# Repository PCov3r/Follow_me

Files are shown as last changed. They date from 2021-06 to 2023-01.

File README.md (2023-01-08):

# Follow me

***Follow me*** est un projet de première année d'école d'ingénieur créé par 9 étudiants.<br>
Le but est de suivre une personne grâce à un algorithme de reconnaissance faciale et de faire du streaming. On utilise ainsi une raspberry, une carte STM32 et 2 servo-moteurs (un pour le pan et un pour le tilt).<br> On a également implémenté un contrôle manuel du tracking par le biais d'API coté serveur et d'une autre raspberry et d'une STM32 coté commande.

## Serveur et streaming

[Section relative au serveur flask et au tracking](WebServer/FlaskServer/)

Nous avons utilisé la librairie OpenCV pour faire du tracking et la librairie Flask pour implémenter le serveur web et le streaming.<br>

### Tracking et API

La librairie OpenCV possède de manière native différents trackers, dont les détails peuvent être trouvés [ici](https://learnopencv.com/object-tracking-using-opencv-cpp-python/) et [ici](https://ehsangazar.com/object-tracking-with-opencv-fd18ccdd7369). Dans notre cas, nous utilisons le tracker KCF qui est non seulement précis, mais qui retrouve également la personne si celle-ci sort et rentre dans le champ de la caméra. <br>
Le passage du mode tracking automatique au mode contrôle manuel est assuré par le biais d'[API](https://flask.palletsprojects.com/en/2.0.x/api/) sous forme de requêtes HTTP. Le serveur Flask reçoit ces requêtes, en analyse les arguments, et agit en conséquence.
<br>
### Communication avec la carte STM32

La communication entre la Raspberry Pi et la carte STM32 gérant la caméra et les servo-moteurs se fait via le protocole [UART](https://www.raspberrypi.org/documentation/configuration/uart.md). Des détails sur le protocole mis en place se trouvent dans la section relative au contrôle des servos.
Il est à noter que le contrôle des mouvements est pour le moment très naïf. En effet, on indique simplement à la STM32 dans quelle direction on souhaite orienter la caméra. 
<br>
Nous avons en effet abandonné l'idée d'indiquer précisément à la carte la position relative de l'utilisateur, ceci pour des raisons de simplicité et surtout de temps.
Une source d'amélioration serait ainsi d'implémenter cela et d'agir en conséquence sur la vitesse de déplacement afin de s'assurer de ne jamais perdre l'utilisateur.
<br>
### Liste des packages à installer pour le serveur web et tracking

pip : ``sudo apt-get install python3-pip`` <br>
imutils : ``pip3 install imutils`` <br>
opencv : ``apt-get install python3-opencv``<br>
flask : ``pip3 install flask``

<br>
<br>

## Contrôle des mouvements de la caméra

[Section relative au contrôle des mouvements de la caméra](/servo/)

### Les servomoteurs (Mouvement pan (axe X) et tilt (axe Y))

Afin de contrôler les servomoteurs qui régissent les mouvements de la caméra, nous avons créé une libraire en C pour traduire les instructions en une série de valeurs que les servomoteurs comprennent.<br>
Les moteurs ont une mémoire (une RAM qui s'efface à chaque mise hors tension et une ROM permanente) dans laquelle nous pouvons stocker des valeurs. Chaque case mémoire contient l'état d'un certain paramètre du moteur : une case stocke l'angle du moteur, une autre stocke sa vitesse et une autre stocke sa température interne par exemple. Ainsi, pour faire tourner le moteur, nous n'envoyons pas "tourne à 120°" mais plutôt "écrit 120° dans la case mémoire qui stocke l'angle du moteur".
<p align="center"><a href="https://emanual.robotis.com/docs/en/dxl/ax/ax-12a/#control-table-of-eeprom-area">Les cases mémoires ainsi que leur fonction sont accessibles ici</a></p>
La librairie permet de faire cette traduction pour facilement commander les moteurs. Nous avons codé presque toutes les fonctions présentes sur le site, pour pouvoir réutiliser cette librairie pour d'éventuels futurs projets.<br>
Maintenant que nous savons <i>quoi</i> envoyer, il faut se demander <i>comment</i>. En effet, la communication avec le moteur ne se fait via qu'un seul fil. Le protocole est donc plutôt simple : <br>
- Tant qu'il ne se passe rien, la sortie de la carte reste à l'état haut (5V).<br>
- Si la carte envoie une instruction, alors la sortie va passer à l'état bas (0V), et à partir de là le moteur va commencer à lire la série de 0 et de 1.<br>
- Le moteur interprète la série binaire, exécute l'action correspondante, puis renvoie à la carte une autre série binaire qui peut être une erreur, la valeur de la case mémoire ou bien un code de bon déroulement.<br>
Ce protocole s'appelle l'Half-Uart (en opposition avec l'Uart qui utilise 2 fils : un pour l'envoi et un pour la réception). <a href="https://emanual.robotis.com/docs/en/dxl/protocol1/">Plus de détails sur la communication avec les moteurs ici</a>.



### Le zoom et le focus de la caméra

Le contrôle du zoom et de la caméra fonctionne exactement comme les moteurs, seul le protocole de comunication change, cette fois-ci c'est l'i2c. Les cases mémoires ainsi que les valeurs [sont décrites ici](https://www.arducam.com/docs/cameras-for-raspberry-pi/ptz-camera/software/). On ajoute aussi la [datasheet de la caméra](https://www.arducam.com/downloads/modules/RaspberryPi_camera/OV5647DS.pdf)


### La communication STM/Raspberry

Enfin, c'est la Raspberry qui s'occupe du tracking du visage, c'est donc elle qui envoie les ordres de mouvements de la caméra. Or, les moteurs sont commandés par la carte STM. Il faut donc établir une communication entre les deux. Nous avons donc établi un code entre nous pour échanger ces instructions, via le protocole Uart.


## Commande manuelle

[Section relative à la commande manuelle du tracking](WebServer/clientSide/)

En plus du tracking, nous avons ajouté à l'utilisateur la possibilité de prendre la main sur le contrôle de la caméra via un boitier de commande relié au serveur principal par API.<br>
Ainsi, grâce à un simple interrupteur, on passe du mode automatique au mode manuel et inversement.
Le contrôle des mouvements selon les axes x et y ainsi que du zoom sont assurés par 2 joysticks. <br> <br>
L'acquisition se fait via une carte STM32, qui communique ces informations à une raspberry via la librairie ``pyserial``. Cette dernière envoie ensuite des requêtes HTTP au serveur Flask via la librairie ``pycurl``.
<br>
De plus amples informations peuvent être trouvées dans les commentaires accompagnant chaque code.
boitier commande

### Liste des packages à installer pour le contrôle manuel de la caméra

pip : ``sudo apt-get install python3-pip`` <br>
pyserial : ``pip3 install pyserial`` <br>
pycurl : ``pip3 install pycurl``

<br>
<br>

## Du POE !
[Section relative au shield POE](/POE/)

Notre cahier des charges imposait également la conception d'un shield POE. <br>
L’objectif de notre Shield POE est de recevoir le courant par un câble ethernet branché à la Raspberry Pi 4B afin d’alimenter cette dernière, mais aussi les moteurs permettant d'orienter la caméra. <br>

**Versioning:** <br>
<br>
* V1 <br>
 La tension fournie par le distributeur POE au travers du câble Ethernet est une tension continue comprise entre 42V et 52V, il nous a donc fallu utiliser deux abaisseurs de tensions afin d’obtenir les tensions de 5V et 11.1V nécessaires respectivement pour l’alimentation de la Raspberry Pi 4B et des moteurs. <br>
La première tension souhaitée est créée à partir de l’abaisseur LM2576HVS (utilisé dans la configuration présentée à la page 19 de la [DataSheet](POE/DataSheet_LM2576HVS.pdf) avec lesvaleurs de composants calculés grâce aux instructions et tables données page 19,20,21). Le montage entourant l’abaisseur 11.1V  LM46002-Q1 est également tiré de sa propre [Datasheet](POE/DataSheet_LM46002-Q1.pdf) page 24. <br>
Les valeurs des composants de ces deux montages retenus apparaissent dans le Schematics du projet EAGLE.

* V2 <br>
 La première version avait pour seul objectif de vérifier que les montages sélectionnés permettaient en effet d’obtenir les tensions désirées. Une fois cela validé, nous avons créé cette deuxième version, comportant les mêmes circuits, mais sur un PCB adapté à la Raspberry Pi 4B. Le shield se fixe directement sur les 4 pins de la Raspberry Pi 4B destinées à la redistribution de l'énergie reçue par le cable ethernet, et sur les pins 2 et 4 (5v), 6 et 9 (GND) pour l’alimentation directe de la Raspberry. Il se fixe également sur les pins 8 et 10 relatives à l'UART afin de communiquer avec les moteurs.
 
 Fonctions | Pins correspondantes
------------ | -------------
Récupérer et redistribuer l'énergie reçue par Ethernet | Pins près du jack Ethernet (POE hat)
Alimenter la Raspberry | 2, 4 (5v) <br> 6, 9 (GND)
Etablir la liaison UART STM/RPi | 8, 10

* V3 <br>
 Nous avons compris lors de la réalisation de la deuxième version du PCB que l’attribution des pins destinées au POE sur la Raspberry dépendent du câble ethernet et de l’injecteur POE utilisés. Afin que notre shield puisse fonctionner correctement avec tous les câbles ethernet et tous les injecteurs POE, nous avons rajouté sur cette version finale un pont de diodes, qui, peu importe l’attribution des pins de la Raspberry Pi 4B, nous garantit une tension positive et une masse.
 
200465168_157028079806266_8768297953444945326_n(1)

**DISCLAIMER:** <br>
La norme POE+ nécessiterait un composant supplémentaire (non implémenté ici) sur le shield pour être utilisable. Ce shield POE n’est donc absolument pas compatible avec la norme POE+, et ne fonctionnera pas si cette norme est sélectionnée dans les paramètres de l’injecteur. (Si vous sélectionnez la norme POE+ avec ce shield POE, l’injecteur délivrera une tension intermittente bien en dessous de la valeur attendue, et sera donc inutilisable.)  Be advised. <br>
La capacité Cin doit selon la datasheet supporter une tension de 100V. Cette dernière est difficile à trouver mais peut être achetée ici: https://fr.farnell.com/tdk/ckg57nx7r2a106m500jh/condensateur-10uf-100v-mlcc-2220/dp/1886985

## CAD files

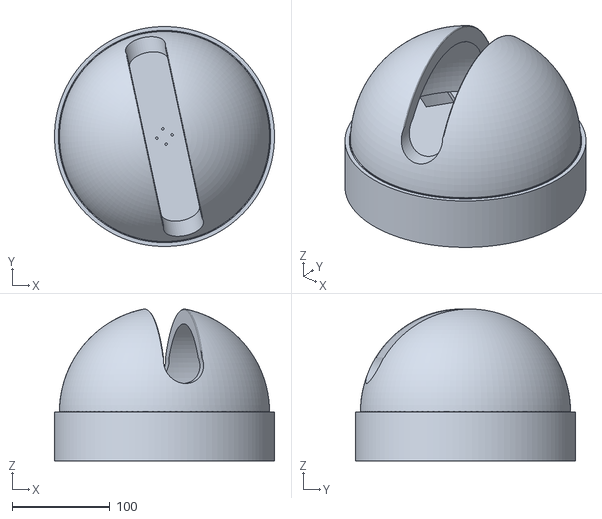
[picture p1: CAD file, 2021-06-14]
Ensemble.stl
225.0 x 224.9 x 155.4

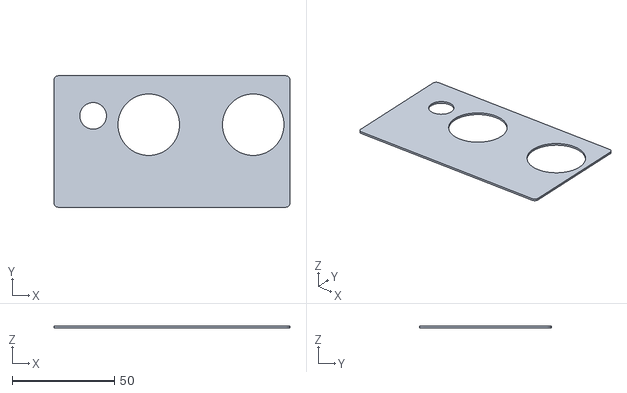
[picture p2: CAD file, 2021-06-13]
Manual command/Top_v3_3D.stl
115.2 x 64.2 x 1.00

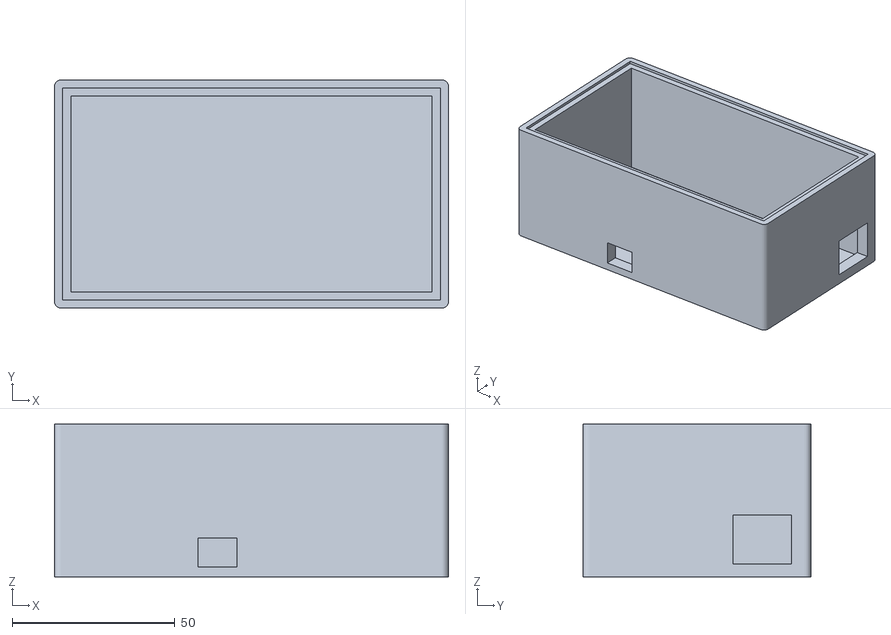
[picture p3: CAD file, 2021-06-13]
Manual command/Box_v3_3D.stl
121.2 x 70.2 x 47.0

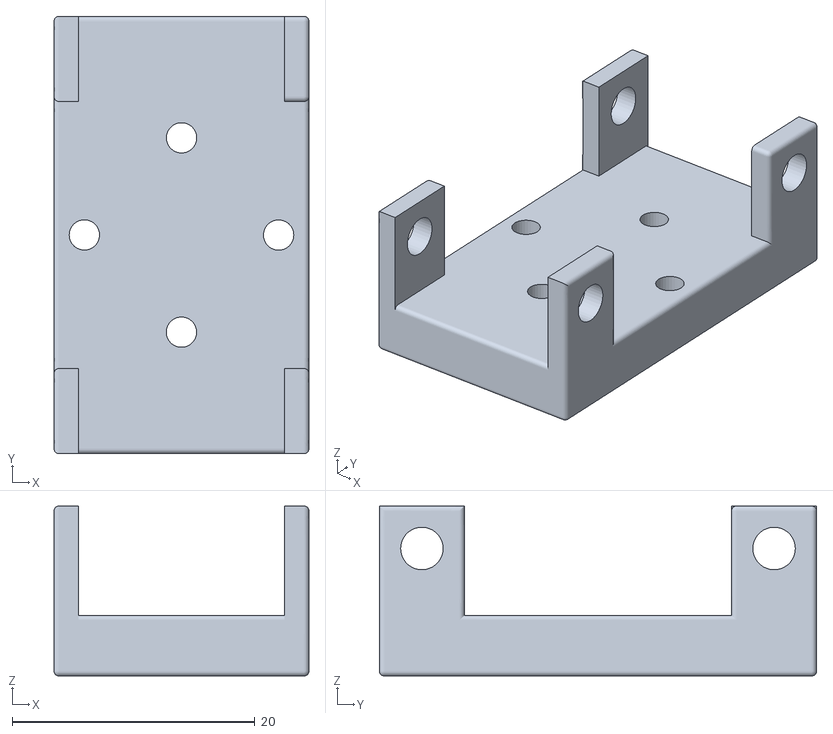
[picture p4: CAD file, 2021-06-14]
Pince v6.stl
21.0 x 36.0 x 14.0

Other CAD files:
Manual command/Box_v3.f3d
Manual command/Top_v3.f3d

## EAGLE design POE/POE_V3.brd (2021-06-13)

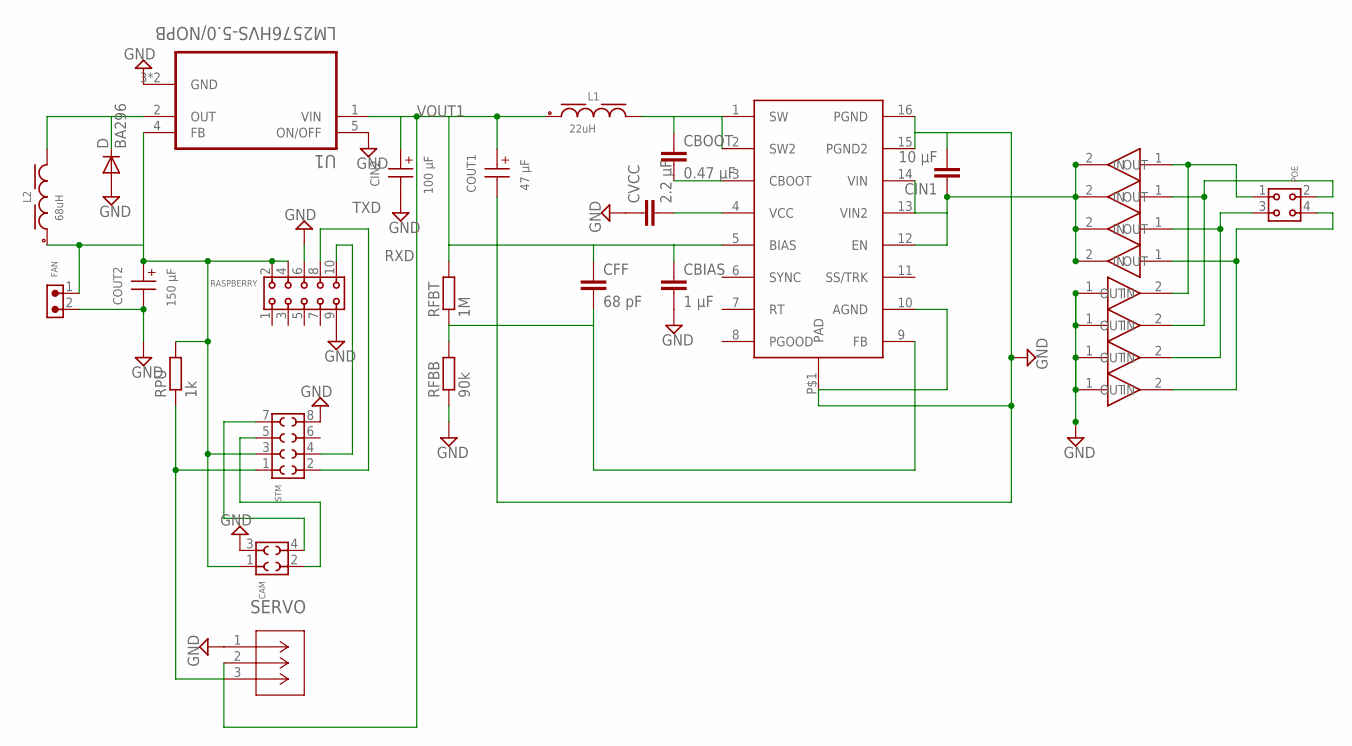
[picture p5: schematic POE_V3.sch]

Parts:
CAM: 6100XX21821_61000421821; 61000421821
CBIAS: 1 µF; C1206
CBOOT: 0.47 µF; C1206
CFF: 68 pF; C1206
CIN1: 10 µF; C2220K
CIN2: 100 µF; WCAP-ASLI_6.3X5.5(DXL)
COUT1: 47 µF; WCAP-ASLI_5X5.5(DXL)
COUT2: 150 µF; WCAP-ASLI_6.3X5.5(DXL)
CVCC: 2.2 µF; C1206
D: BA296; P2-15
FAN: 6130XX11021_61300211021; 61300211021
L1: 22uH; WE-PD_1260
L2: 68uH; WE-PD_1210
POE: 6130XX21821_61300421821; 61300421821
RASPBERRY: 6130XX21821_61301021821; 61301021821
RFBB: 90k; M1206
RFBT: 1M; M1206
RPU: 1k; M1206
SERVO: 22035035; CON_22035035
STM: 6100XX21821_61000821821; 61000821821
U1: LM2576HVS-5.0/NOPB; VREG_TPS79625KTTR
U$1: LM46002; TSSOP16
U$2, U$3, U$4, U$5, U$6, U$7, U$8, U$9: RGF1D

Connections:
GND: CAM.3, CBIAS.2, CIN1.2, CIN2.2 (-), COUT1.2 (-), COUT2.2 (-), CVCC.1, D.A, FAN.2, RASPBERRY.6, RASPBERRY.9, RFBB.1, SERVO.1, STM.8, U1.3 (GND), U1.5 (ON/OFF), U1.6 (GND), U$1.10 (AGND), U$1.15 (PGND2), U$1.16 (PGND), U$1.P$1 (PAD), U$4.1 (IN), U$5.1 (IN), U$8.1 (IN), U$9.1 (IN)
unnamed: CBOOT.1, L1.2, U$1.1 (SW), U$1.2 (SW2)
unnamed: CBOOT.2, U$1.3 (CBOOT)
unnamed: CVCC.2, U$1.4 (VCC)
unnamed: POE.1, U$2.1 (IN), U$4.2 (OUT)
unnamed: POE.2, U$3.1 (IN), U$5.2 (OUT)
unnamed: D.C, L2.2, U1.2 (OUT)
unnamed: CAM.4, STM.7
unnamed: CAM.2, STM.5
unnamed: RPU.1, SERVO.3, STM.1
unnamed: POE.3, U$6.1 (IN), U$8.2 (OUT)
unnamed: POE.4, U$7.1 (IN), U$9.2 (OUT)
RFBT: CFF.2, RFBB.2, RFBT.1, U$1.9 (FB)
RXD: RASPBERRY.10, STM.4
TXD: RASPBERRY.8, STM.2
VIN: CIN1.1, U$1.12 (EN), U$1.13 (VIN2), U$1.14 (VIN), U$2.2 (OUT), U$3.2 (OUT), U$6.2 (OUT), U$7.2 (OUT)
VOUT1: CBIAS.1, CFF.1, CIN2.1 (+), COUT1.1 (+), L1.1, RFBT.2, SERVO.2, U1.1 (VIN), U$1.5 (BIAS)
VOUT2: CAM.1, COUT2.1 (+), FAN.1, L2.1, RASPBERRY.2, RASPBERRY.4, RPU.2, STM.3, U1.4 (FB)

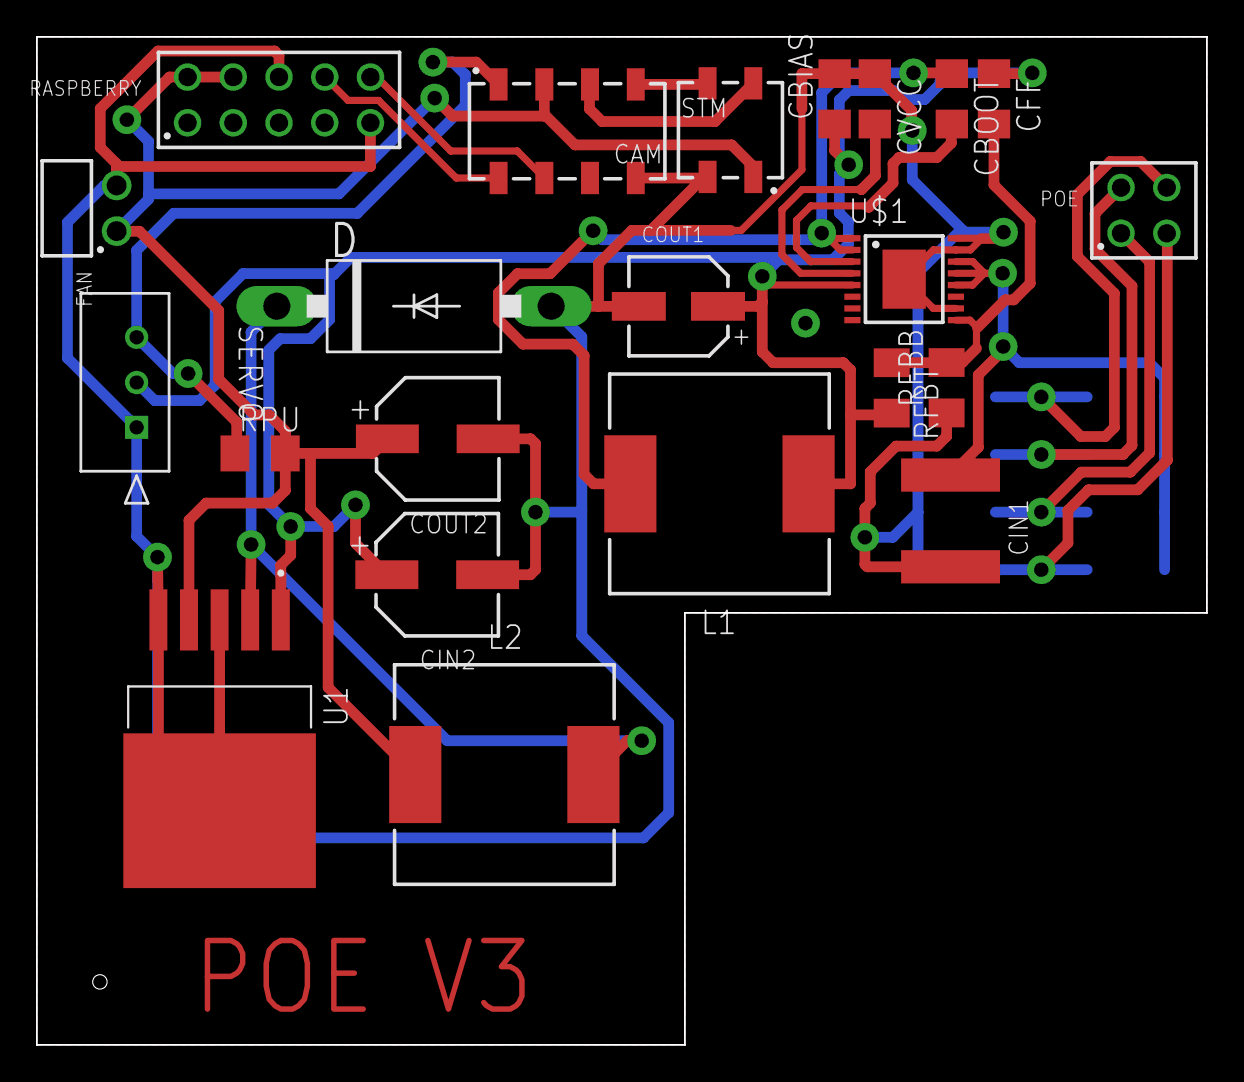
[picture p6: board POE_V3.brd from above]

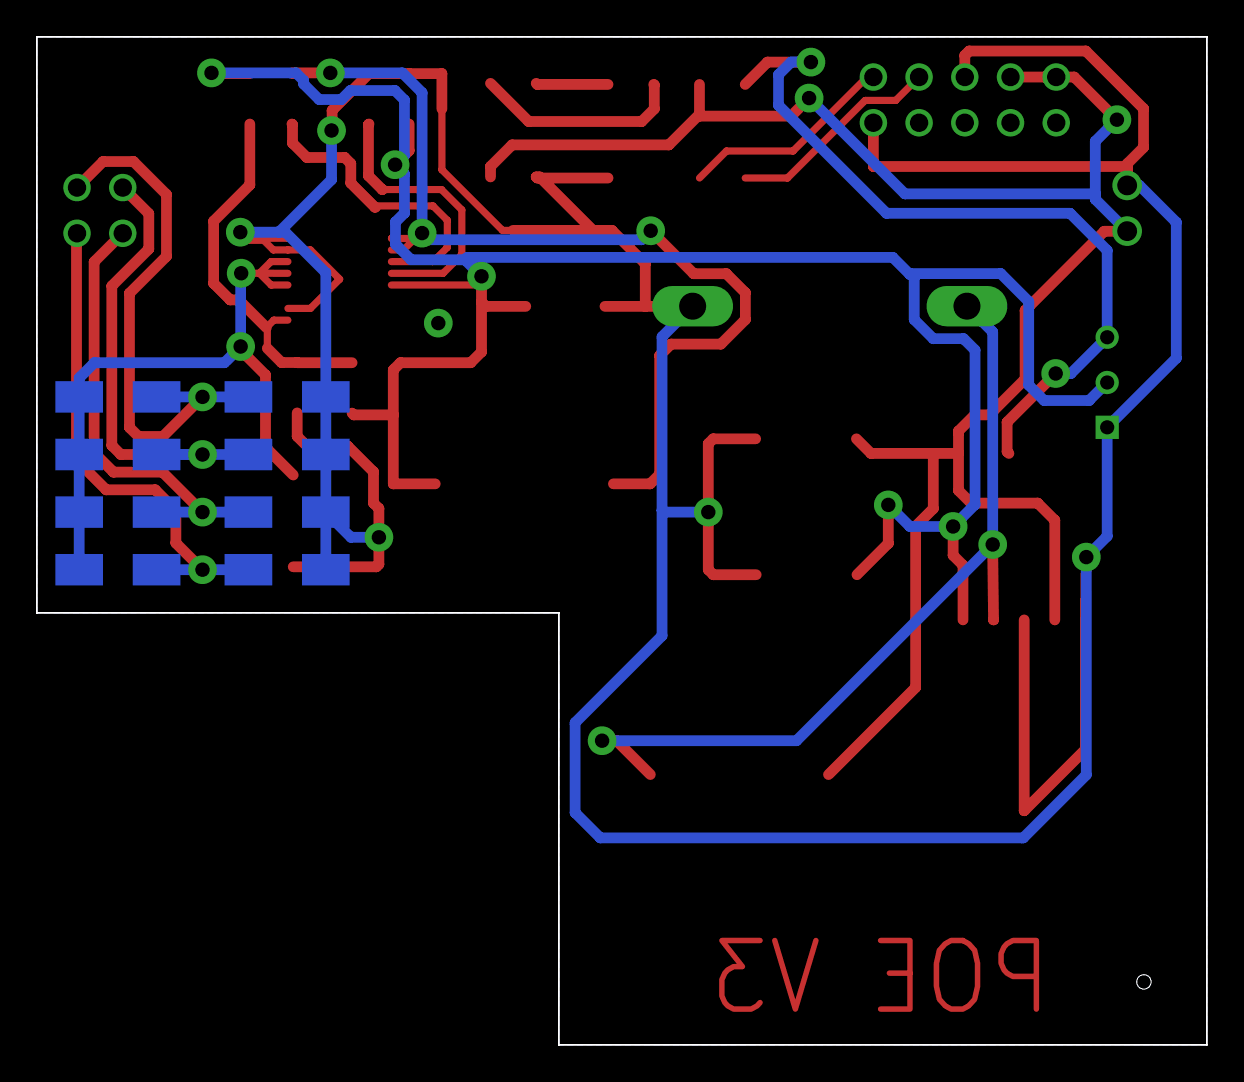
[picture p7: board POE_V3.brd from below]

Board: 2 copper layers, 65.0 x 56.0 mm, 30 parts (8 on the bottom side), 18 nets.

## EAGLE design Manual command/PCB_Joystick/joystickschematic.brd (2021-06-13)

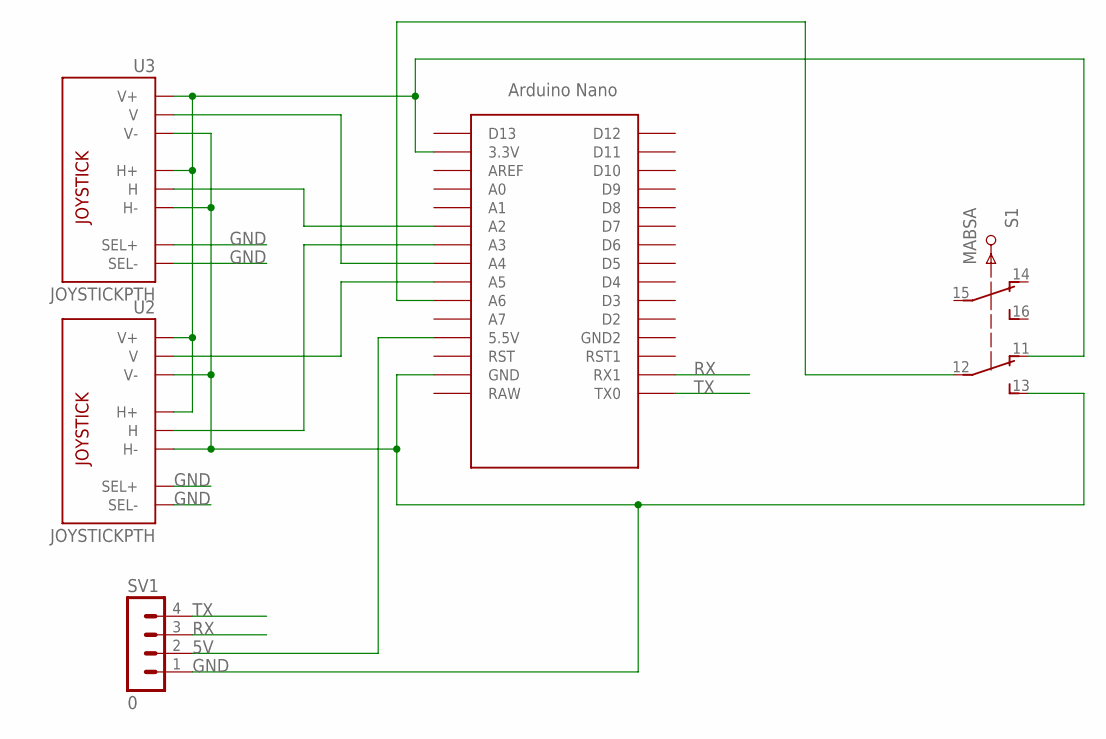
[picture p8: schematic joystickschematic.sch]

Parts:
S1: MABSA
SV1: 0; MA04-1
U2, U3: JOYSTICKPTH; JOYSTICK
U$2: NANO

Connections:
3.3V: S1.11, U2.H1 (H+), U2.V1 (V+), U3.H1 (H+), U3.V1 (V+), U$2.3.3V
5V: SV1.2, U$2.5V (5.5V)
GND: S1.13, SV1.1, U2.B1A (SEL+), U2.B2A (SEL-), U2.H3 (H-), U2.V3 (V-), U3.B1A (SEL+), U3.B2A (SEL-), U3.H3 (H-), U3.V3 (V-), U$2.GND
unnamed: U3.V2 (V), U$2.A4
unnamed: U3.H2 (H), U$2.A2
unnamed: U2.H2 (H), U$2.A3
unnamed: U2.V2 (V), U$2.A5
unnamed: S1.12, U$2.A6
RX: SV1.3, U$2.RX1
TX: SV1.4, U$2.TX0

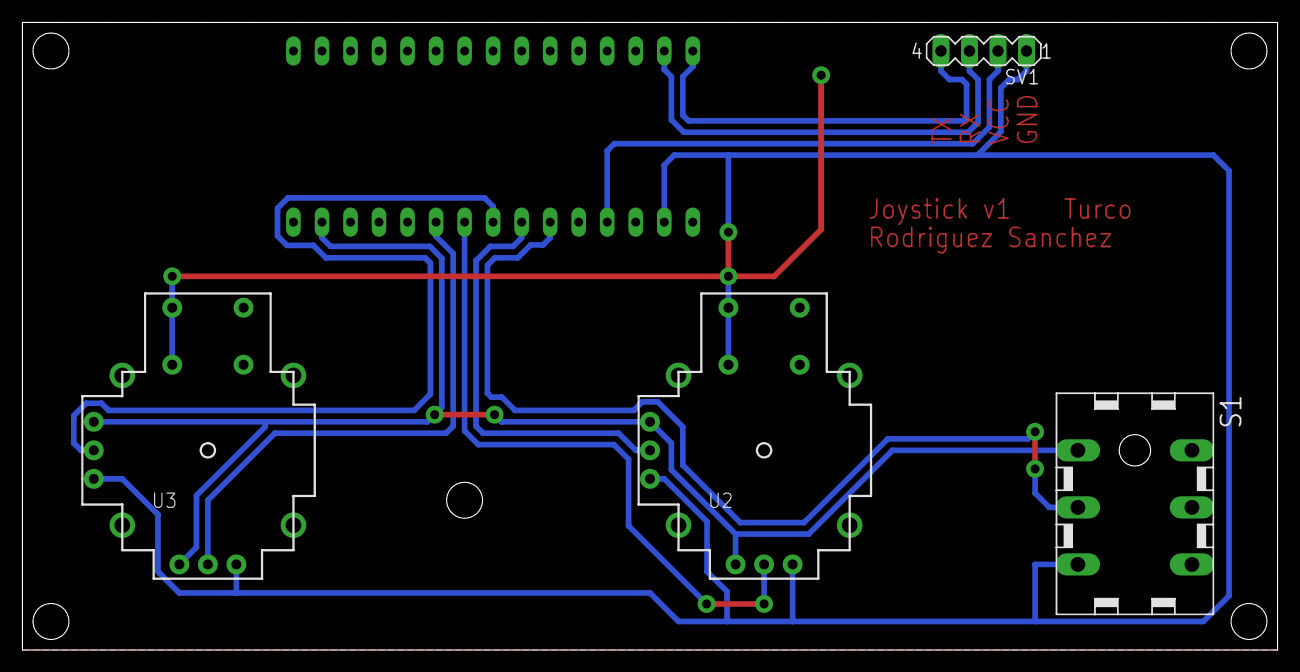
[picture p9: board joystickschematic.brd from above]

Board: 2 copper layers, 111.8 x 55.9 mm, 5 parts (0 on the bottom side), 10 nets.

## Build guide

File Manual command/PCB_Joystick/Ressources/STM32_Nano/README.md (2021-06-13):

# Arduino-Eagle-Cad-Library
Eagle Cad Library for Arduino Mini and Nano
This is an Eagle Cad Library that contains Arduino nano and Arduino pro Mini pin outs.

It gives you a single part that can be placed on a schematic/board so you can simply solder in or plug in 
an Arduino pro mini or nano into your project.

v1.3 Corrected several cosmetic issues and Added a pinout for the StepStick Stepper Controler.

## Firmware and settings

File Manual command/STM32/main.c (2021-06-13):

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
/* Includes ------------------------------------------------------------------*/
#include "main.h"

/* USER CODE BEGIN Includes */
#include <string.h>
#include <stdio.h>
/* USER CODE END Includes */

ADC_HandleTypeDef hadc1;
UART_HandleTypeDef huart1;
UART_HandleTypeDef huart2;

void SystemClock_Config(void);
static void MX_GPIO_Init(void);
static void MX_USART2_UART_Init(void);
static void MX_ADC1_Init(void);
static void MX_USART1_UART_Init(void);


int main(void)
{
  /* USER CODE BEGIN 1 */
uint16_t j1x;
uint16_t j1y;
uint16_t j2y;
int sw=0;
char msg[16];
char msg2[13];
char msg3[13];
char msg4[17];
  /* USER CODE END 1 */

  /* MCU Configuration--------------------------------------------------------*/

  /* Reset of all peripherals, Initializes the Flash interface and the Systick. */
  HAL_Init();

  /* Configure the system clock */
  SystemClock_Config();

  /* Initialize all configured peripherals */
  MX_GPIO_Init();
  MX_USART2_UART_Init();
  MX_ADC1_Init();
  MX_USART1_UART_Init();

  /* USER CODE BEGIN 2 */

  void ADC_Select_CH8 (void){
	  ADC_ChannelConfTypeDef sConfig = {0};
  	  sConfig.Channel = ADC_CHANNEL_8;
  	  sConfig.Rank = ADC_REGULAR_RANK_1;
  	  sConfig.SamplingTime = ADC_SAMPLETIME_2CYCLES_5;
  	  sConfig.SingleDiff = ADC_SINGLE_ENDED;
  	  sConfig.OffsetNumber = ADC_OFFSET_NONE;
  	  sConfig.Offset = 0;
  	  if (HAL_ADC_ConfigChannel(&hadc1, &sConfig) != HAL_OK)
  	  {
  	    Error_Handler();
  	  }
  }

  void ADC_Select_CH10 (void){
	  ADC_ChannelConfTypeDef sConfig = {0};
  	  sConfig.Channel = ADC_CHANNEL_10;
  	  sConfig.Rank = ADC_REGULAR_RANK_1;
  	  sConfig.SamplingTime = ADC_SAMPLETIME_2CYCLES_5;
  	  sConfig.SingleDiff = ADC_SINGLE_ENDED;
  	  sConfig.OffsetNumber = ADC_OFFSET_NONE;
  	  sConfig.Offset = 0;
  	  if (HAL_ADC_ConfigChannel(&hadc1, &sConfig) != HAL_OK)
  	  {
  	    Error_Handler();
  	  }
  }

  void ADC_Select_CH11 (void){
	  ADC_ChannelConfTypeDef sConfig = {0};
  	  sConfig.Channel = ADC_CHANNEL_11;
  	  sConfig.Rank = ADC_REGULAR_RANK_1;
  	  sConfig.SamplingTime = ADC_SAMPLETIME_2CYCLES_5;
  	  sConfig.SingleDiff = ADC_SINGLE_ENDED;
  	  sConfig.OffsetNumber = ADC_OFFSET_NONE;
  	  sConfig.Offset = 0;
  	  if (HAL_ADC_ConfigChannel(&hadc1, &sConfig) != HAL_OK)
  	  {
  	    Error_Handler();
  	  }
  }
  /* USER CODE END 2 */

  /* Infinite loop */
  /* USER CODE BEGIN WHILE */
  while (1)
  {

	      // Get ADC value for horizontal position 'j1x' (joystick 1, axis x)

        //Select channel corresponding to horizontal position of joystick 1
	  	  ADC_Select_CH8();
        //Enable ADC and starts conversion of the chosen channel
	  	  HAL_ADC_Start(&hadc1);
        //Poll for regular conversion complete
	  	  HAL_ADC_PollForConversion(&hadc1, 1000);
        //Gets the converted value from data register and saves it in j1x
	  	  j1x = HAL_ADC_GetValue(&hadc1);
        //Disables ADC and stops conversion of chosen channel
	  	  HAL_ADC_Stop(&hadc1);

        // Get ADC value for vertical position 'j1y' (joystick 1, axis y)

		    ADC_Select_CH10();
			  HAL_ADC_Start(&hadc1);
			  HAL_ADC_PollForConversion(&hadc1, 1000);
			  j1y = HAL_ADC_GetValue(&hadc1);
			  HAL_ADC_Stop(&hadc1);

        // Get ADC value for zoom level 'j2y' (joystick 2, axis y)

	  	  ADC_Select_CH11();
	  	  HAL_ADC_Start(&hadc1);
	  	  HAL_ADC_PollForConversion(&hadc1, 1000);
	  	  j2y = HAL_ADC_GetValue(&hadc1);
	  	  HAL_ADC_Stop(&hadc1);

        // Get value for switch position 'sw'
	  	  if (HAL_GPIO_ReadPin(GPIOA,GPIO_PIN_7)){
	  		  sw=1;
	  	  }
	  	  else{
	  		  sw=0;
	  	  }

	      // Convert to string
	      sprintf(msg, "%4d",j1x);
	      sprintf(msg2, "%4d",j1y);
	      sprintf(msg3, "%4d",j2y);
	      sprintf(msg4, "%4d",sw);

        // Concatenate to one string
	      strcat(msg,msg2);
	      strcat(msg,msg3);
	      strcat(msg,msg4);

        // Sending to Raspberry
        HAL_UART_Transmit(&huart1, (uint8_t*)msg, strlen(msg), 1000);

        // Sending to PC via USB (for tests)
	      // HAL_UART_Transmit(&huart2, (uint8_t*)msg, strlen(msg), 1000);


	      // Pretend we have to do something else for a while
	      HAL_Delay(500);

  }
  /* USER CODE END WHILE */

}

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


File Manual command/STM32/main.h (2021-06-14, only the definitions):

#define MCO_Pin GPIO_PIN_0
#define MCO_GPIO_Port GPIOA
#define VCP_TX_Pin GPIO_PIN_2
#define VCP_TX_GPIO_Port GPIOA
#define SWDIO_Pin GPIO_PIN_13
#define SWDIO_GPIO_Port GPIOA
#define SWCLK_Pin GPIO_PIN_14
#define SWCLK_GPIO_Port GPIOA
#define VCP_RX_Pin GPIO_PIN_15
#define VCP_RX_GPIO_Port GPIOA
#define LD3_Pin GPIO_PIN_3
#define LD3_GPIO_Port GPIOB

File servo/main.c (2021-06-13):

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
/* Includes ------------------------------------------------------------------*/
#include "main.h"

/* USER CODE BEGIN Includes */
#include <stdio.h>
#include "servo.h"

/* USER CODE END Includes */

/* USER CODE BEGIN PD */
#define UART_RX_BUFFER_SIZE 6
#define UART_TX_BUFFER_SIZE 6
/* USER CODE END PD */

I2C_HandleTypeDef hi2c2;

TIM_HandleTypeDef htim1;

UART_HandleTypeDef huart4;
UART_HandleTypeDef huart2;
UART_HandleTypeDef huart3;
DMA_HandleTypeDef hdma_usart3_rx;

/* USER CODE BEGIN PV */
uint8_t rx_buffer[UART_RX_BUFFER_SIZE];
uint8_t tx_buffer[UART_TX_BUFFER_SIZE];

int uart_rx_it = 0; // Variable to track the state of DMA register.
unsigned char X, Y, Z, F, F1, F2; // Variables to contain the instructions sent by the Raspberry.
/* USER CODE END PV */

void SystemClock_Config(void);
static void MX_GPIO_Init(void);
static void MX_DMA_Init(void);
static void MX_TIM1_Init(void);
static void MX_USART3_UART_Init(void);
static void MX_USART2_UART_Init(void);
static void MX_UART4_Init(void);
static void MX_I2C2_Init(void);
/**
  * @brief  The application entry point.
  * @retval int
  */
int main(void)
{
  /* MCU Configuration--------------------------------------------------------*/

  /* Reset of all peripherals, Initializes the Flash interface and the Systick. */
  HAL_Init();

  /* Configure the system clock */
  SystemClock_Config();

  /* Initialize all configured peripherals */
  MX_GPIO_Init();
  MX_DMA_Init();
  MX_TIM1_Init();
  MX_USART3_UART_Init(); // UART 3 is used to communicate with the Raspberry Pi.
  MX_USART2_UART_Init(); // UART 2 is used to communicate with a PC (serial port).
  MX_UART4_Init(); // UART 4 is used to control the motors.
  MX_I2C2_Init(); // I2C2 is used to control the camera.
  /* USER CODE BEGIN 2 */
  HAL_TIM_Base_Start(&htim1);
  /* USER CODE END 2 */

  /* Infinite loop */
  /* USER CODE BEGIN WHILE */
  HAL_UART_Receive_DMA(&huart3, rx_buffer, UART_RX_BUFFER_SIZE); // The DMA register now stocks everything that comes from UART 3 in rx_buffer, and will be full with UART_RX_BUFFER_SIZE values. 
  setGoalPosition(ID_Y, 0, &huart4); // Reset motors position to Y=0 and X=150. 
  setGoalPosition(ID_X, 150, &huart4);
  focus(&hi2c2, 0x4C, 1); // Reset the focus value for a clear image at the start.
  HAL_Delay(1000); // Slight delay to let the motors reset to their positions.
  while (1)
  {

	  if(uart_rx_it==1){ // When the DMA register is full, it means the program received a complete set of instructions from the Raspberry Pi.
		  X = rx_buffer[0];
		  Y = rx_buffer[1];
		  Z = rx_buffer[2];
		  F1 = rx_buffer[3];
		  F2 = rx_buffer[4];
		  if(X==3) moveStep(ID_X, 1, &huart4); // Moves CCW on X-axis.
		  if(X==2) moveStep(ID_X, -1, &huart4); // Moves CW on X-axis.
		  if(Y==4) moveStep(ID_Y, -1, &huart4); // Moves CCW on Y-axis.
		  if(Y==5) moveStep(ID_Y, 1, &huart4); // Moves CW on Y-axis.
		  if(Z==0) zoomrel(&hi2c2, -1); // Zooms out.
		  if(Z==1) zoomrel(&hi2c2, 1); // Zooms in.
		  if(F1 =! 0xFF) focus(&hi2c2, F1, F2); // Set the focus (range between 0 and 0x4E20).
		  uart_rx_it = 0; // Once the instruction is read, the program waits until the DMA is full again.
	}
  }

    /* USER CODE END WHILE */

}

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
/* USER CODE BEGIN 4 */

void HAL_UART_RxCpltCallback(UART_HandleTypeDef *huart) // If the DMA register is full, this function is called.
{
	uart_rx_it = 1; // This flag switches to 1 to read the instruction in the main program.
}

void delay_us(int us){
	__HAL_TIM_SET_COUNTER(&htim1,0);
	while(__HAL_TIM_GET_COUNTER(&htim1)<us);
}

/* USER CODE END 4 */
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


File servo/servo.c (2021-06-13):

#include "servo.h"

/**
 * 	@brief Send a series of hex values to motors, and store the feedback.
 * 	@note This function is only used in the other functions of the library.
 * 	@param packet Pointer to sending data buffer (unsigned char*).
 * 	@param lenPacket Amount of data to be transfered.
 * 	@param lenFeedback Amount of data to be received.
 * 	@param huart Pointer to an UART_HandleTypeDef structure that contains the configuration information for the specified UART.
 * 	@param feedback Pointer to receiving data buffer (unsigned char*).
 */
void sendPacket(unsigned char* packet, int lenPacket, int lenFeedback, UART_HandleTypeDef* huart, unsigned char* feedback){
	HAL_HalfDuplex_EnableTransmitter(huart);
	HAL_UART_Transmit(huart, packet, lenPacket, 1000);
	HAL_HalfDuplex_EnableReceiver(huart);
	HAL_UART_Receive(huart, feedback, lenFeedback, 10);
}
/**
 * @brief Change the ID of the motor.
 * @param ID_target ID of the motor to be changed.
 * @param ID_goal New ID of the motor (0-255).
 * @param huart Pointer to an UART_HandleTypeDef structure that contains the configuration information for the specified UART.
 */
void setID(unsigned char ID_target, unsigned char ID_goal, UART_HandleTypeDef* huart){

	unsigned char packet[8];
	unsigned char feedback[6];

	packet[0] = HEADER;
	packet[1] = HEADER;
	packet[2] = ID_target;
	packet[3] = L_WRITE;
	packet[4] = WRITE;
	packet[5] = A_ID;
	packet[6] = ID_goal;
	packet[7] = checksum(packet, sizeof(packet));
	sendPacket(packet, 8, 6, huart, feedback);
	}

/**
 * @brief Change the communication speed of the motors.
 * @note Base speed is 1 million bps.
 * @param ID ID of the motor.
 * @param Brate New baud rate (int), check documentation for speed values.
 * @param huart Pointer to an UART_HandleTypeDef structure that contains the configuration information for the specified UART.
 */
void setBaudRate(unsigned char ID, int BRate, UART_HandleTypeDef* huart){

	unsigned char packet[8];
	unsigned char feedback[6];

	packet[0] = HEADER;
	packet[1] = HEADER;
	packet[2] = ID;
	packet[3] = L_WRITE;
	packet[4] = WRITE;
	packet[5] = A_COM_S;
	packet[6] = BRate;
	packet[7] = checksum(packet, sizeof(packet));

	sendPacket(packet, 8, 6, huart, feedback);
}

/**
 * @brief Change the time between receiving a packet and returning the feedback (from the motor)
 * @note The real return delay time is given by delay*2us.
 * @note The base delay value is 250 (500us).
 * @param ID ID of the motor.
 * @param delay New delay value, between 0 and 254.
 * @param huart Pointer to an UART_HandleTypeDef structure that contains the configuration information for the specified UART.
 */
void setReturnDelayTime(unsigned char ID, int delay, UART_HandleTypeDef* huart){

	unsigned char packet[8];
	unsigned char feedback[6];

	packet[0] = HEADER;
	packet[1] = HEADER;
	packet[2] = ID;
	packet[3] = L_WRITE;
	packet[4] = WRITE;
	packet[5] = A_RET_D;
	packet[6] = delay;
	packet[7] = checksum(packet, sizeof(packet));

	sendPacket(packet, 8, 6, huart, feedback);
}

/**
 * @brief Change the minimum angle possible on the motor.
 * @note The base value is 0.
 * @param ID ID of the motor.
 * @param angle New minimum angle, in degrees.
 * @param huart Pointer to an UART_HandleTypeDef structure that contains the configuration information for the specified UART.
 */
void setMinAngleLimit(unsigned char ID, float angle, UART_HandleTypeDef* huart){

	unsigned char packet[9];
	unsigned char feedback[6];
	int MinPos, MinPos1, MinPos2;

	MinPos = angle/STEP;
	MinPos1 = MinPos%256;
	MinPos2 = MinPos/256;

	packet[0] = HEADER;
	packet[1] = HEADER;
	packet[2] = ID;
	packet[3] = 0x05;
	packet[4] = WRITE;
	packet[5] = A_CW_AL;
	packet[6] = MinPos1;
	packet[7] = MinPos2;
	packet[8] = checksum(packet, sizeof(packet));

	sendPacket(packet, 9, 6, huart, feedback);
}

/**
 * @brief Change the maximum angle possible on the motor.
 * @note The base value is 300.
 * @param ID ID of the motor.
 * @param angle New minimum angle, in degrees.
 * @param huart Pointer to an UART_HandleTypeDef structure that contains the configuration information for the specified UART.
 */
void setMaxAngleLimit(unsigned char ID, float angle, UART_HandleTypeDef* huart){

	unsigned char packet[9];
	unsigned char feedback[6];
	int MaxPos, MaxPos1, MaxPos2;

	MaxPos = angle/STEP;
	MaxPos1 = MaxPos%256;
	MaxPos2 = MaxPos/256;

	packet[0] = HEADER;
	packet[1] = HEADER;
	packet[2] = ID;
	packet[3] = 0x05;
	packet[4] = WRITE;
	packet[5] = A_CW_AL;
	packet[6] = MaxPos1;
	packet[7] = MaxPos2;
	packet[8] = checksum(packet, sizeof(packet));

	sendPacket(packet, 9, 6, huart, feedback);
}

/**
 *@brief Change the maximum working temperature of the motor.
 *@note If the internal temperature of the motor is higher than the limit, the motor will shut down automatically.
 *@param ID ID of the motor.
 *@param temp Range : 0 - 100, 1°C per unit.
 *@param huart Pointer to an UART_HandleTypeDef structure that contains the configuration information for the specified UART.
 */
void setTemperatureLimit(unsigned char ID, int temp, UART_HandleTypeDef* huart){

	unsigned char packet[8];
	unsigned char feedback[6];

	packet[0] = HEADER;
	packet[1] = HEADER;
	packet[2] = ID;
	packet[3] = L_WRITE;
	packet[4] = WRITE;
	packet[5] = A_TLIM;
	packet[6] = temp;
	packet[7] = checksum(packet, sizeof(packet));

	sendPacket(packet, 8, 6, huart, feedback);
}

/**
 *@brief Change the minimum voltage threshold for the motor to start.
 *@note If the voltage supply is lower than this value, the motor won't start.
 *@note The actual voltage threshold is given by V/10 Volts.
 *@param ID ID of the motor.
 *@param V Int value between 50 and 160.
 *@param huart Pointer to an UART_HandleTypeDef structure that contains the configuration information for the specified UART.
 */
void setMinimunVolt(unsigned char ID, int V, UART_HandleTypeDef* huart){

	unsigned char packet[8];
	unsigned char feedback[6];

	packet[0] = HEADER;
	packet[1] = HEADER;
	packet[2] = ID;
	packet[3] = L_WRITE;
	packet[4] = WRITE;
	packet[5] = A_MINV;
	packet[6] = V;
	packet[7] = checksum(packet, sizeof(packet));

	sendPacket(packet, 8, 6, huart, feedback);
}

/**
 *@brief Change the maximum voltage threshold for the motor to start.
 *@note If the voltage supply is higher than this value, the motor won't start.
 *@note The actual voltage threshold is given by V/10 Volts.
 *@param ID ID of the motor.
 *@param V Int value between 50 and 160.
 *@param huart Pointer to an UART_HandleTypeDef structure that contains the configuration information for the specified UART.
 */
void setMaximunVolt(unsigned char ID, int V, UART_HandleTypeDef* huart){

	unsigned char packet[8];
	unsigned char feedback[6];

	packet[0] = HEADER;
	packet[1] = HEADER;
	packet[2] = ID;
	packet[3] = L_WRITE;
	packet[4] = WRITE;
	packet[5] = A_MAXV;
	packet[6] = V;
	packet[7] = checksum(packet, sizeof(packet));

	sendPacket(packet, 8, 6, huart, feedback);
}
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

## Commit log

2021-04-20 Create Tracker_position.py
    Ce script inclut en plus de l'autocorrection le calcul de la position de la personne par rapport à la caméra.
2021-06-12 Created UART communication library
2021-06-12 Update and rename video.py to camera.py
2021-06-13 Added 3D models
    [Box_v3.f3d, Box_v3_3D.stl, Top_v3.f3d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]

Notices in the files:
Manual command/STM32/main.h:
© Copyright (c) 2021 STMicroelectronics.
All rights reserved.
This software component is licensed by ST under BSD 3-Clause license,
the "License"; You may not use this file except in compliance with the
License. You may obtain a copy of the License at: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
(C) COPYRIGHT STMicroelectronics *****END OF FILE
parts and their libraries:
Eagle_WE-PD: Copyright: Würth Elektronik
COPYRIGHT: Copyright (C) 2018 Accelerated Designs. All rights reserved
